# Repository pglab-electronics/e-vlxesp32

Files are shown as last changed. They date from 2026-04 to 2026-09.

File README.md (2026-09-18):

# E-VLXESP32

<p align="center">
  <picture>
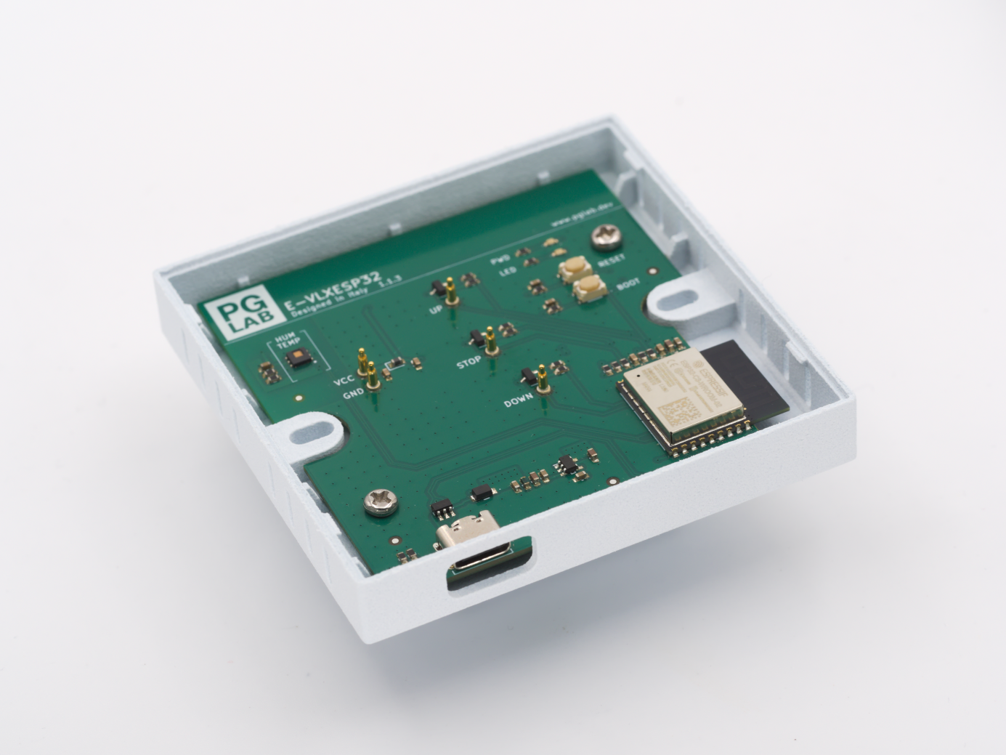
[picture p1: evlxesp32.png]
E-VLXESP32
    
  </picture>
</p>

**E-VLXESP32** is an ESP32-based electronics module by **PG LAB Electronics** designed to control **VELUX®** motorized skylight windows using original **VELUX®** wall remotes.

## About

The **E-VLXESP32** is a compact electronics module featuring an integrated **temperature and humidity sensor**.

It connects to battery-powered **VELUX®** wall remote controls (models **KLI311, KLI312, KLI313**) and allows you to control **VELUX®** motorized skylight windows over your **local Wi-Fi network**.

The E-VLXESP32 is available in two versions:

- Standard Version – Designed to fit standard 501 wall boxes and powered directly from the 220V AC mains supply for permanent installation.
- KIT Version - Powered exclusively via USB-C. This version requires user assembly and a 3D-printed enclosure using the provided design files.

This repository contains the ESPHome YAML configuration files used to build and customize the E-VLXESP32 firmware.

## Features

- Local Wi-Fi control of **VELUX® wall remotes**
- Full window control: open, close, or stop
- Powered by **ESPHome**
- Built-in **temperature** and **humidity** sensor
- No cloud needed
- Snap-fit design, no soldering required
- No batteries required
- Fits standard 501 wall boxes

## How It Works

The device interfaces with supported VELUX® wall remotes using pogo pins that make contact with the remote’s internal control pads. The ESP32 exposes these controls over Wi-Fi using ESPHome, allowing integration with systems like Home Assistant.

## Connect to Wi-Fi

Follow one of the methods below to connect your device to Wi-Fi.

### Method A — Hotspot (easiest, no app required)

1. Open Wi-Fi settings on your phone or computer.
2. Connect to the network “E-VLXESP32 Hotspot”.
3. A captive portal page should open automatically.
   If it doesn’t, open your browser and go to 192.168.4.1.
4. Enter your Wi-Fi name and password.
5. The device will connect, and the hotspot will disappear.

### Method B — Bluetooth via Home Assistant app

1. pen the Home Assistant mobile app (iOS or Android).
2. Go to Settings → Devices & Services.
3. Look for a “Discovered” banner at the top.
   If you don’t see it, make sure Bluetooth is enabled.
4. Tap E-VLXESP32 and follow the steps to enter your Wi-Fi credentials.

### Method C — USB-C serial

1. Connect the device to your computer using a USB-C cable.
2. Open the ESPHome dashboard.
3. Follow the prompts to provision the device via serial.

## Getting Started

If you want to flash the firmware directly from your computer and configure your Wi-Fi credentials and passwords.

### Requirements
- ESPHome installed
- E-VLXESP32 hardware module
- Supported VELUX® remote (KLI311, KLI312, KLI313)

### Installation

1. Clone this repository:
   ```bash
   git clone https://github.com/pglab-electronics/e-vlxesp32.git
   
2. Open the YAML configuration in ESPHome

3. Update:
   - Wi-Fi credentials
   - Device name
   - Home Assistant API Encryption Key
   - Over The Air update Password
   - Optional sensor settings

4. Flash to the ESP32:
   ```bash
   esphome run evlxesp32.yaml

## Pairing

Before snap-fitting the E-VLXESP32, make sure you can operate your skylight window. Follow the standard **VELUX®** remote pairing procedure to link your remote (KLI311, KLI312, or KLI313) with the window before using the E-VLXESP32.

## Repository Structure

- `evlxesp32.yaml` – Main ESPHome configuration
- `secrets.yaml` – Wi-Fi credentials, passwords, and keys
- `firmware` - Build of the last firmware
  - `firmware.factory.bin` - Firmware ready to flash at offset 0x0
  - `firmware.ota.bin` - Firmware for over the air update
  - `firmware.md5` - Firmware md5 hash
- `stl` - 3D enclosure model

## Hardware

STANDARD VERSION

| Component | Description |
| ----------- | ------------- |
| MCU | ESP32-C3 (ESP32-C3-WROOM-02-N4) |
| Ambient Sensor | HDC1080 |
| Pogo Pins | for KLI311,KLI312, KLI313 connection |
| Programming Port | USB-C |
| AC-DC Module (*) | IRM-01-5 |
| Power Input (*) | 220AC, 60Hz screw terminal |
| Power Input USB (**) | 5 VDC, From USB-C port |
| Power Consumption (**) | 50 mA |

(*) Only for STANDARD VERSION

(**) Only for KIT VERSION

## Pinout

| GPIO | Function | Direction |
| ------ | ---------- | ----------- |
| GPIO3 | I2C SDA | Input/Output |
| GPIO2 | I2C SCL | Output |
| GPIO1 | POGO PIN DOWN (shutter) | Output |
| GPIO7 | POGO PIN STOP (shutter) | Output |
| GPIO5 | POGO PIN UP (shutter) | Output |
| GPI10 | USER LED GREEN | Output |
| GPIO4 | POGO PIN UP (binary sensor) | Input |
| GPIO6 | POGO PIN STOP (binary sensor) | Input |
| GPIO0 | POGO PIN DOWN (binary sensor) | Input |

## 3D Printing Guidelines KIT

For best results, print the kit version enclosure using **PETG** filament with a **0.2 mm** layer height and **30%** infill. **PETG** is recommended for its slight flexibility and durability, 
which helps achieve a reliable snap-fit assembly and long-term mechanical stability.

Supports are required for all parts to guarantee clean overhangs and a precise final geometry, ensuring the enclosure can snap-fit properly with the **VELUX®** remote cover.

The model is designed with tight tolerances for a precise fit. Depending on your printer calibration, you may need to slightly scale the enclosure up or down if the fit is too tight or too loose.

If the fit is too tight, avoid forcing the **VELUX®** cover onto the enclosure, as excessive pressure may damage or break the snap-fit mechanism.

## License

This project is licensed under the GNU GENERAL PUBLIC LICENSE 3.0 — see [LICENSE](LICENSE) for details.

The ESPHome configuration is open source and free to modify.

## Safety

⚠️ Ensure power is disconnected before installing the module. Incorrect installation may damage the device or connected equipment.

## Disclaimer

The **E-VLXESP32** is an independent third-party product developed and manufactured by PG LAB Electronics S.R.L.S. It is not affiliated with, endorsed by, or sponsored by VELUX A/S or any of its subsidiaries or affiliates.
**VELUX®** is a registered trademark of its respective owner. All references to VELUX® products, including compatible remote control models, are made solely for the purpose of indicating compatibility.
Compatibility is limited to specifically listed **VELUX®** remote control models (**KLI311, KLI312, KLI313**). We do not guarantee compatibility with any other devices or future product revisions.
This product is intended for installation by individuals with appropriate technical knowledge. Improper installation or use may result in damage to equipment or personal injury. The manufacturer assumes no liability for damages arising from incorrect installation or misuse.
By using this product, you acknowledge and accept these terms.

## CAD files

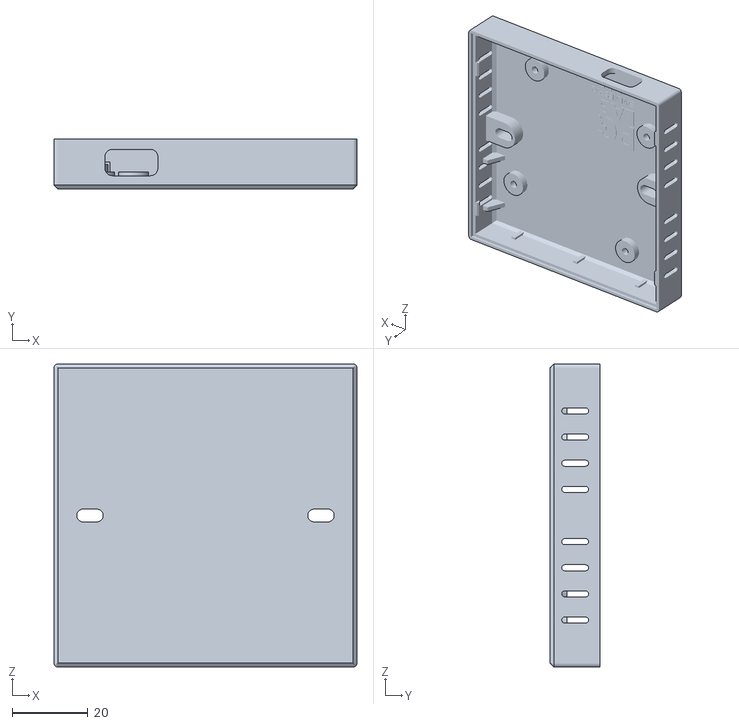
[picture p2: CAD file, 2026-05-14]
stl/evlxesp32_enclosure_kit.stl
80.0 x 13.1 x 80.0

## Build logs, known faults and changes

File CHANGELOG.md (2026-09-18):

# 2026.1.3
- Updated ESPHome version to 2026.9.0
- Added user configurable opening and closing times

# 2026.1.2
- Make it ready for Made for ESPhome

# 2026.1.1
- First version of E-VLXESP32 firmware

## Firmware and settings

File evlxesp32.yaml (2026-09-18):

substitutions:
  device_name: "e-vlxesp32"
  friendly_name: "E-VLXESP32"
  project_name: "PG_LAB_Electronics.E-VLXESP32"
  project_version: "2026.1.3"

esphome:

  name: "${device_name}"
  name_add_mac_suffix: true
  friendly_name: "${friendly_name}"
  project:
    name: "${project_name}"
    version: "${project_version}"

  on_boot: 
    - priority: 200 
      then: 
        - lambda: |- 
            id(shutter).set_open_duration( static_cast<uint32_t>(id(shutter_open_time).state * 1000.0f) );
            id(shutter).set_close_duration( static_cast<uint32_t>(id(shutter_close_time).state * 1000.0f) );   

esp32:
  board: esp32-c3-devkitm-1
  framework:
    type: esp-idf

api:

ota:
  - platform: esphome
    id: ota_esphome
  - platform: http_request
    id: ota_http_request

dashboard_import:
  package_import_url: github://pglab-electronics/e-vlxesp32/evlxesp32.yaml@main
  import_full_config: true

wifi:
  ap:
    ssid: "${friendly_name} Hotspot"

logger:

improv_serial:

esp32_improv:
  authorizer: none

update:
  - platform: http_request
    id: firmware_update
    name: E-VLXESP32 Firmware update
    source: https://pglab-electronics.github.io/e-vlxesp32/manifest.json
    disabled_by_default: false
    update_interval: 6h


time:
  - platform: homeassistant
    id: ha_time

http_request:
  timeout: 10s

captive_portal:

web_server:
  port: 80

i2c:
  sda: GPIO3
  scl: GPIO2
  scan: true
  id: bus_a

sensor:
  - platform: hdc1080
    id: ambient_sensor
    temperature:
      name: "Temperature"
      filters:
       - offset: -2.6
    humidity:
      name: "Humidity"
    address: 0x40
    update_interval: 60s

number: 
  - platform: template 
    id: shutter_open_time 
    name: "Shutter Open Time" 
    icon: "mdi:timer-outline" 
    min_value: 5 
    max_value: 120 
    step: 1 
    unit_of_measurement: "s" 
    mode: box 
    optimistic: true 
    restore_value: true 
    initial_value: 30 
    set_action: 
      - lambda: |- 
          id(shutter).set_open_duration( static_cast<uint32_t>(x * 1000.0f) );

  - platform: template 
    id: shutter_close_time 
    name: "Shutter Close Time" 
    icon: "mdi:timer-outline" 
    min_value: 5 
    max_value: 120 
    step: 1 
    unit_of_measurement: "s" 
    mode: box 
    optimistic: true 
    restore_value: true 
    initial_value: 30 
    set_action: 
      - lambda: |- 
          id(shutter).set_close_duration( static_cast<uint32_t>(x * 1000.0f) );
    
switch:
  - platform: gpio
    name: "Down"
    id: velux_down
    icon: "mdi:window-shutter"
    pin: 
      number: GPIO1
    on_turn_on:
     - delay: 200ms
     - switch.turn_off: velux_down
    interlock: [velux_up, velux_stop]
    internal: true

  - platform: gpio
    name: "Stop"
    id: velux_stop
    icon: "mdi:window-shutter"
    pin: 
      number: GPIO7
    on_turn_on:
     - delay: 200ms
     - switch.turn_off: velux_stop
    interlock: [velux_down, velux_up]
    internal: true

  - platform: gpio
    name: "Up"
    id: velux_up
    icon: "mdi:window-shutter"
    pin: 
     number: GPIO5
    on_turn_on:
     - delay: 200ms
     - switch.turn_off: velux_up
    interlock: [velux_down, velux_stop]
    internal: true

  - platform: gpio
    id: user_led
    pin: GPIO10
    name: "Led Green"
    internal: false

binary_sensor:
  - platform: gpio
    id: sense_up
    pin:
      number: GPIO04
      mode:
        input: true
        pullup: true
    filters:
      - lambda: !lambda return !(x || id(velux_up).state);
    on_press:
      then:
        - cover.open: shutter
  - platform: gpio
    id: sense_stop
    pin:
      number: GPIO06
      mode:
        input: true
        pullup: true
    filters:
      - lambda: !lambda return !(x || id(velux_stop).state);
    on_press:
      then:
        - cover.stop: shutter
  - platform: gpio
    id: sense_down
    pin:
      number: GPIO00
      mode:
        input: true
        pullup: true
    filters:
      - lambda: !lambda return !(x || id(velux_down).state);
    on_press:
      then:
        - cover.close: shutter

cover:
  - platform: time_based
    id: shutter
    name: "Shutter"
    has_built_in_endstop: true
    manual_control: true
    assumed_state: true

    open_action:
      - switch.turn_on: velux_up
    open_duration: 30s

    close_action:
      - switch.turn_on: velux_down
    close_duration: 30s

    stop_action:
      - switch.turn_on: velux_stop

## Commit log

2026-01-07 Adding device YAML file
2026-04-28 Add device picture
2026-04-28 re-upload device picture
2026-05-05 Enhance README with Wi-Fi connection methods
    Added methods to connect the device to Wi-Fi, including Hotspot, Bluetooth via Home Assistant app, and USB-C serial. Updated the pairing section for clarity.
2026-05-14 adding kit 3d model
    [evlxesp32_enclosure_kit.stl]
2026-05-14 added 3d print guidelines
